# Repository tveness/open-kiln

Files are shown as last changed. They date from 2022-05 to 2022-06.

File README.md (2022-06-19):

# Open source kiln 

This project has grown out of the design (and hopefully construction in the near
future) of a kiln for heat-treating 80CrV2 steel.

The project is divided into two main parts: the driver circuit, and the kiln
itself. The driver circuit is assembled from readily-available modules arranged
on a custom PCB (we have a few spares and are happy to post you one of them),
whose design files and production-ready gerbers are in the repository.
The 

All designs are open: copying and improving is not only allowed, but encouraged.

## Driver circuit

### PCB

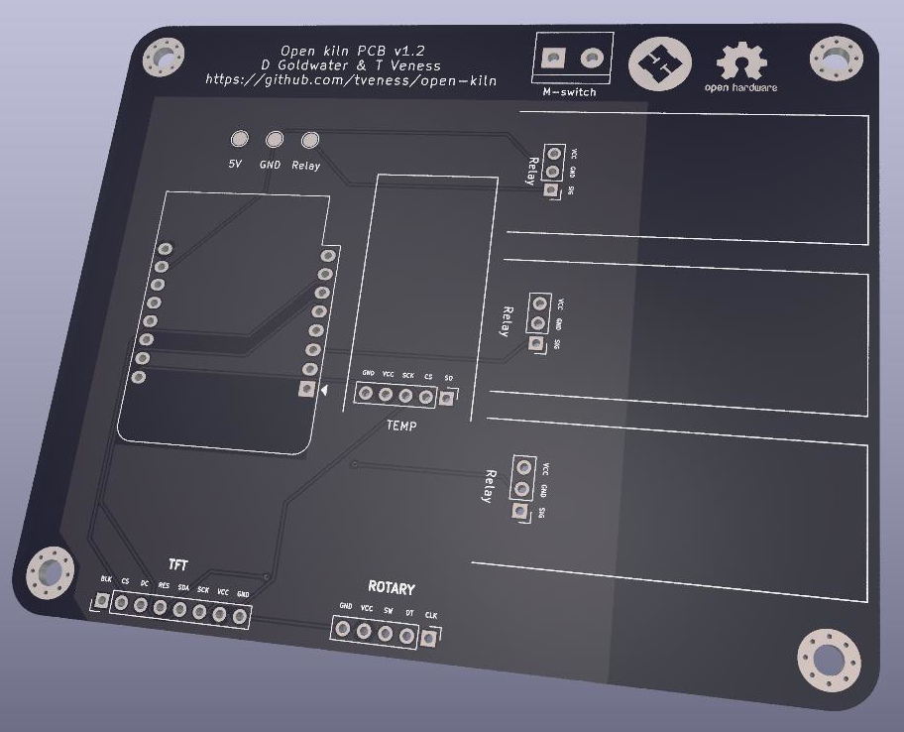
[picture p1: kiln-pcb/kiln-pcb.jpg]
Rendered PCB


We chose to use readily available modules both for protoyping purposes, and also
so reproduction is easy: the modules can all be purchased cheaply and the whole
assembly requires only through-hole soldering skills.

The components used are:

* Wemos D1 mini ESP8266 --- logic and power for board
* MAX6675 temperature module --- converts voltage from K-type thermocouple into signal which can be processed by ESP8266
* Rotary encoder --- input with rotating left and right, and depressing
* 0.96" TFT display
* 3x 5V relay modules

Some of these modules may come with headers already soldered, in which case you
may have to desolder and re-solder appropriate headers (all headers on PCB are
2.54mm/0.1" headers).

The PCB was designed with Kicad.

The logic of the design is that the temperature module measures the temperature
inside the kiln, and then according to the settings (TFT + rotary encoder
interface) the relays are activated to regulate the kiln temperature.

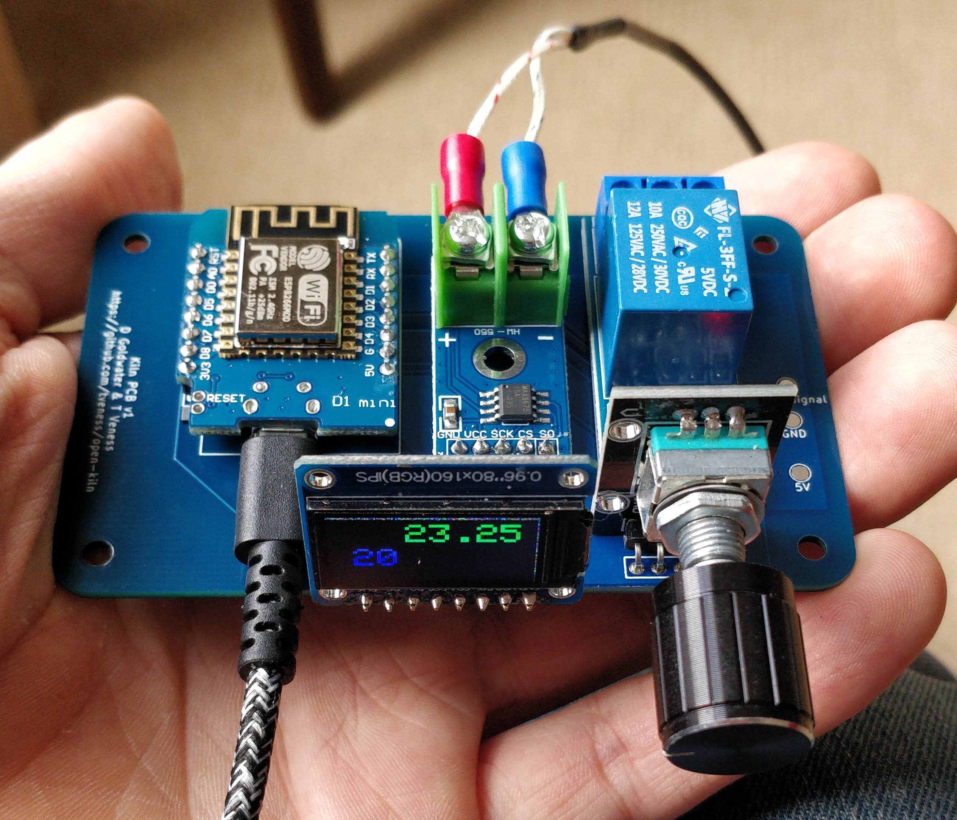
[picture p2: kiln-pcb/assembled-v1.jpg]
Assembled PCB (v1)


### Software

## Physical kiln

### Materials
We will need 27 vermiculite bricks for the main oven. 

### Firebrick enclosure
This is to be made from vermiculite firebricks. These are supplied in Imperial measurements; each brick has dimension:
$$ 8 \times 1 \times 4 ''.$$
The firebrick enclosure is to consist of two parts: the oven cavity, and a door. The measurements of these are as follows:

**Oven**:
Interior: $16 \times 8 \times 6''$

Exterior: $10 \times 17 \times 8$

**Door**:
The door is to be two bricks thick. The dimensions are:
$2 \times 10 \times 8$.

### Plaster casing
The plan is to cast a set of thick sheets with which to encase the oven. Since the door will be two bricks thick, there will be no outer casing for the door. The dimensions for these are to be:

Walls($\times 2$): $17 \times 10 \times d$

floor / ceiling ($\times 2$): $(17+d)\times(8+2d)\times d$

back ($\times 1$): $(8 + 2d)\times 10\times d$

where $d$ gives the thickness for the sheets. Provisionally, this is set at $1.5$''. 

### Approach 1:
Mix vermiculite to quick-set cement in a ratio $4:1$, add water until you can squeeze a fist and get a few drops out. 

### Metal case

### Resistive Elements
We use A1 kanthal wire, sourced from [here](https://www.ebay.co.uk/itm/322024532921). This has a resistivity of $1.8\Omega / m$. Aiming for $R = 13.2 \Omega$ per coil, we calculate:
$$d = 13.2 / 1.8 \\ = 7.3 $$
So that each element ought to be 7.3 $m$ long. 

### Wiring diagram
These images temporary, to be replaced
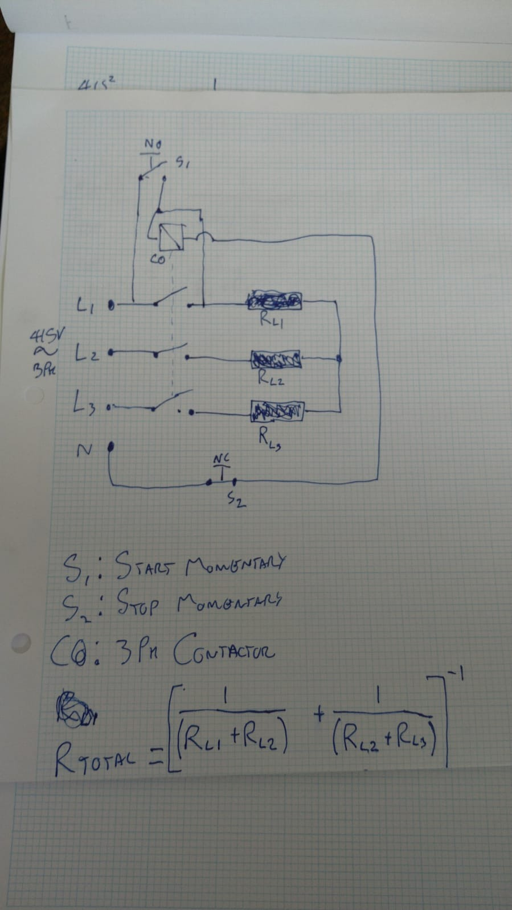
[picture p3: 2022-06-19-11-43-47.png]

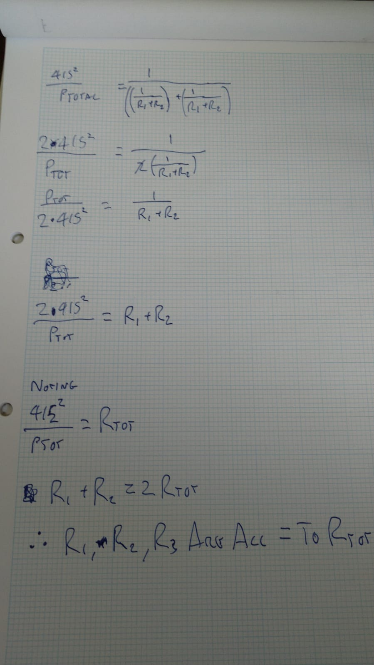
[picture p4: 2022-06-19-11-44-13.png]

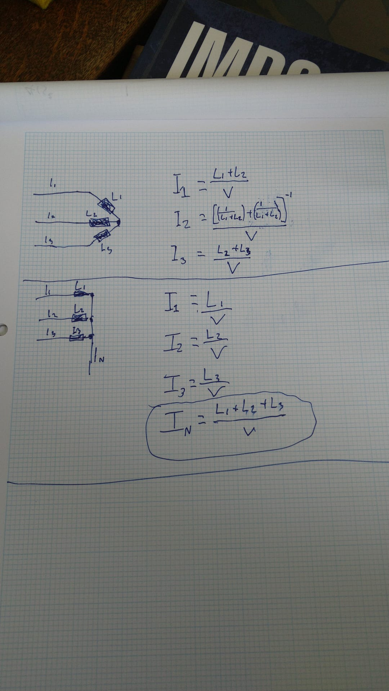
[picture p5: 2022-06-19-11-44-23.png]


### Safety considerations
We are to use:
- MCBs on each resistor element to isolate those in case of a short circuit. Also if one of the other coils fails, the power draw on the remaining coils would increase - the MCB here would save those coils before they burn out.
- Magnetic switch; this will leave a circuit *open* when the oven door is open, and *closed* when the oven door is closed. This means that there should be no power to the heating elements when the door is open. 
- Connector: This would function as a relay switch for the three phase power
- Relay: This would act as a pre-relay, and would be controlled directly by the PCB. (Expand this section)

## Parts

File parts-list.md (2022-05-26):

Electronics

* ESP8266 Wemos D1 mini
* MAX6675 temperature module
* Relay module
* TFT display 0.96"
* Rotary encoder

Kiln
* Kanthal wire
* Firebricks
* Metal enclosure

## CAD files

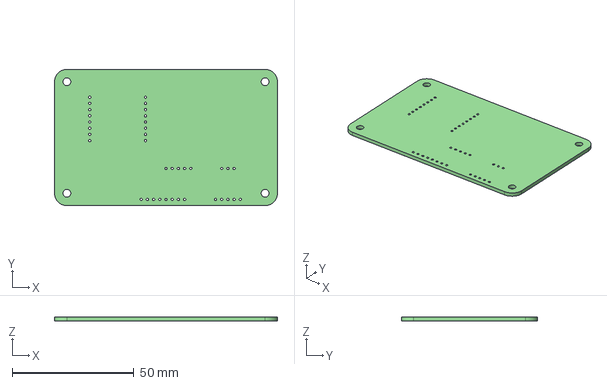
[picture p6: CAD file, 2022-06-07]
kiln-pcb/kiln-pcb.step
91.4 x 55.9 x 1.60 mm

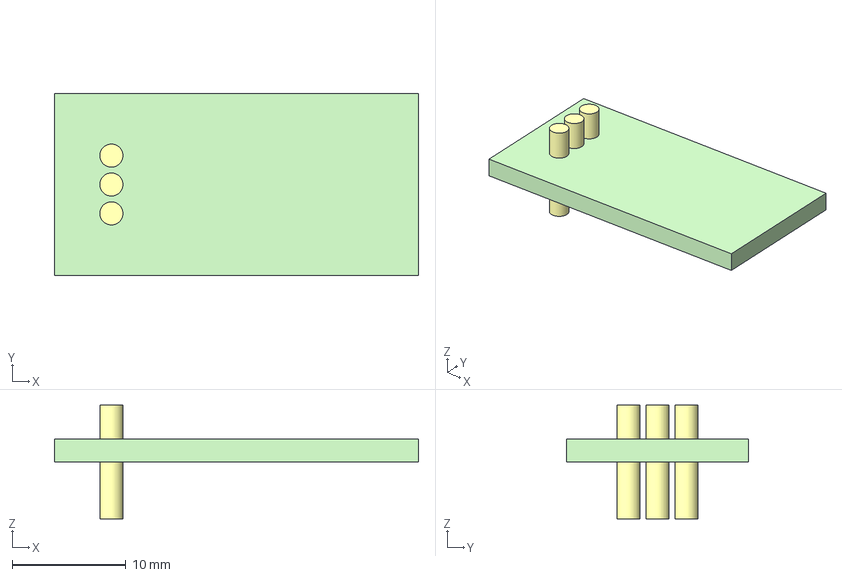
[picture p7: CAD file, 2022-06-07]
kiln-pcb/models/temp.FCStd
32.0 x 16.0 x 10.0 mm

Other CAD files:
kiln-pcb/models/temp-body.step

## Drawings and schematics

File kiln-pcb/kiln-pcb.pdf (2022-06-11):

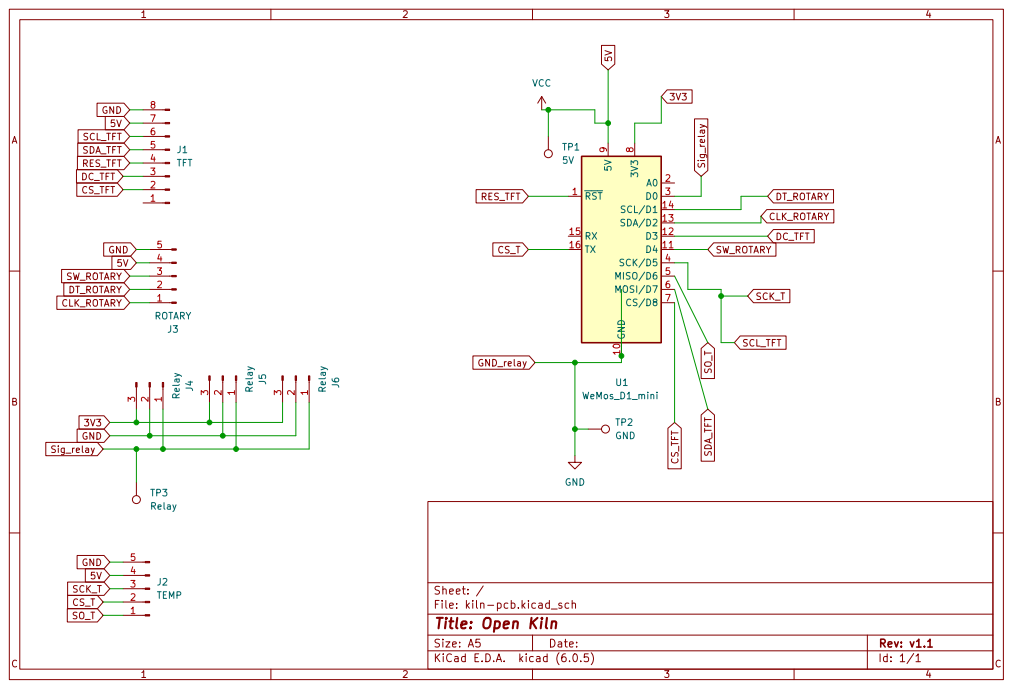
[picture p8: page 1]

File: kiln-pcb.kicad_sch Sheet: / 12345

Id: 1/1 Title: Open Kiln

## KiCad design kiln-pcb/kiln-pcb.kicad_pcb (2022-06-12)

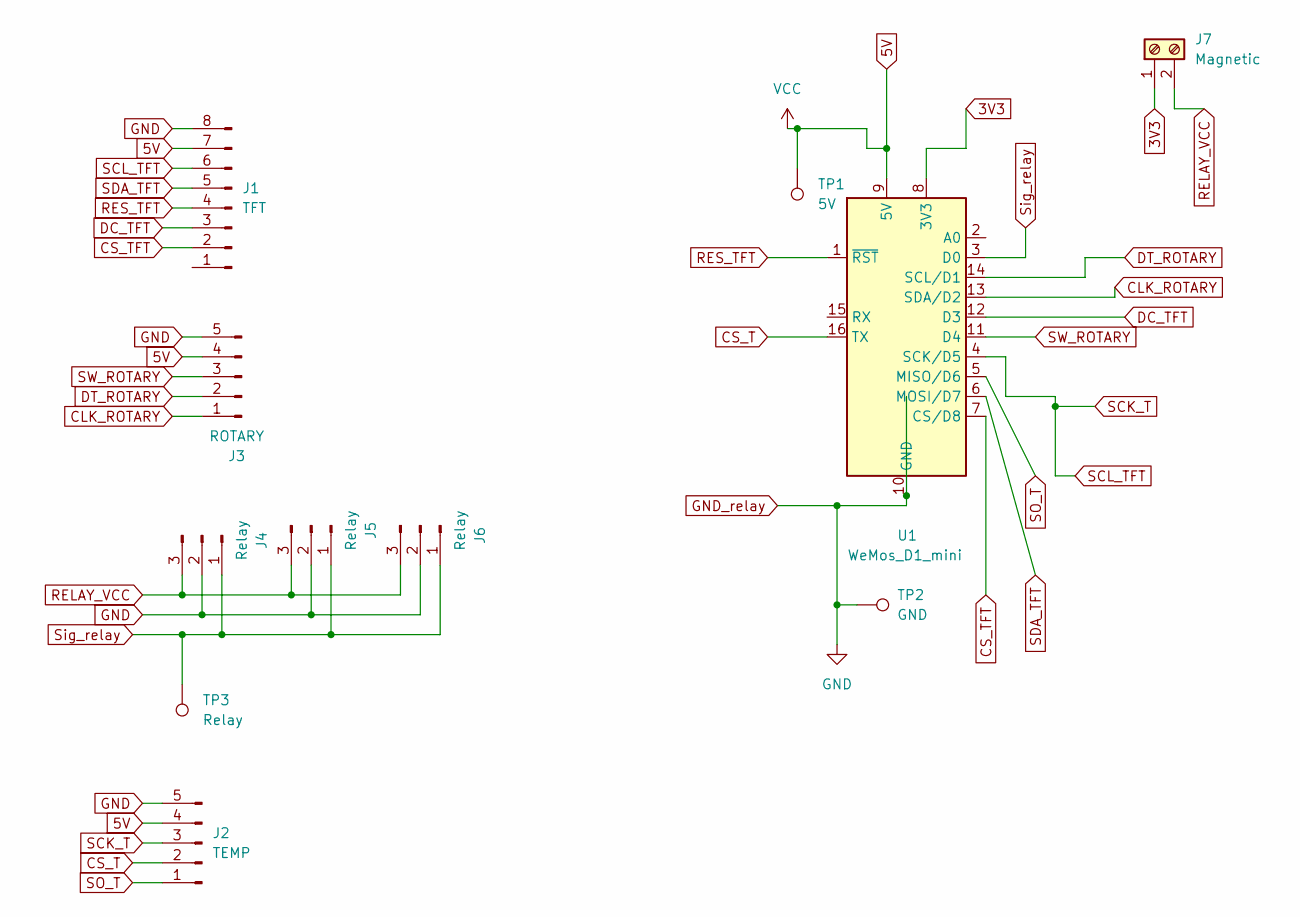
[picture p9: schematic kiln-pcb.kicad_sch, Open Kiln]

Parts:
J1: TFT; PinHeader_1x08_P2.54mm_Vertical
J2: TEMP; PinHeader_1x05_P2.54mm_Vertical
J3: ROTARY; PinHeader_1x05_P2.54mm_Vertical
J4, J5, J6: Relay; PinHeader_1x03_P2.54mm_Vertical
J7: Magnetic; TerminalBlock_bornier-2_P5.08mm
TP1: 5V; TestPoint_Pad_D2.0mm
TP2: GND; TestPoint_Pad_D2.0mm
TP3: Relay; TestPoint_Pad_D2.0mm
U1: WeMos_D1_mini; WEMOS_D1_mini_light

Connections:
3V3: J7.1, U1.8 (3V3); also elsewhere on the board
5V: J1.7, J2.4, J3.4, TP1.1, U1.9 (5V)
CLK_ROTARY: J3.1, U1.13 (SDA/D2)
CS_T: J2.2, U1.16 (TX)
CS_TFT: J1.2, U1.7 (CS/D8)
DC_TFT: J1.3, U1.12 (D3)
DT_ROTARY: J3.2, U1.14 (SCL/D1)
GND: J1.8, J2.5, J3.5, J4.2, J5.2, J6.2, TP2.1, U1.10 (GND)
RELAY_VCC: J4.3, J5.3, J6.3, J7.2; also elsewhere on the board
RES_TFT: J1.4, U1.1 (~RST)
SCK_T: J1.6, J2.3, U1.4 (SCK/D5)
SDA_TFT: J1.5, U1.6 (MOSI/D7)
SO_T: J2.1, U1.5 (MISO/D6)
SW_ROTARY: J3.3, U1.11 (D4)
Sig_relay: J4.1, J5.1, J6.1, TP3.1, U1.3 (D0)

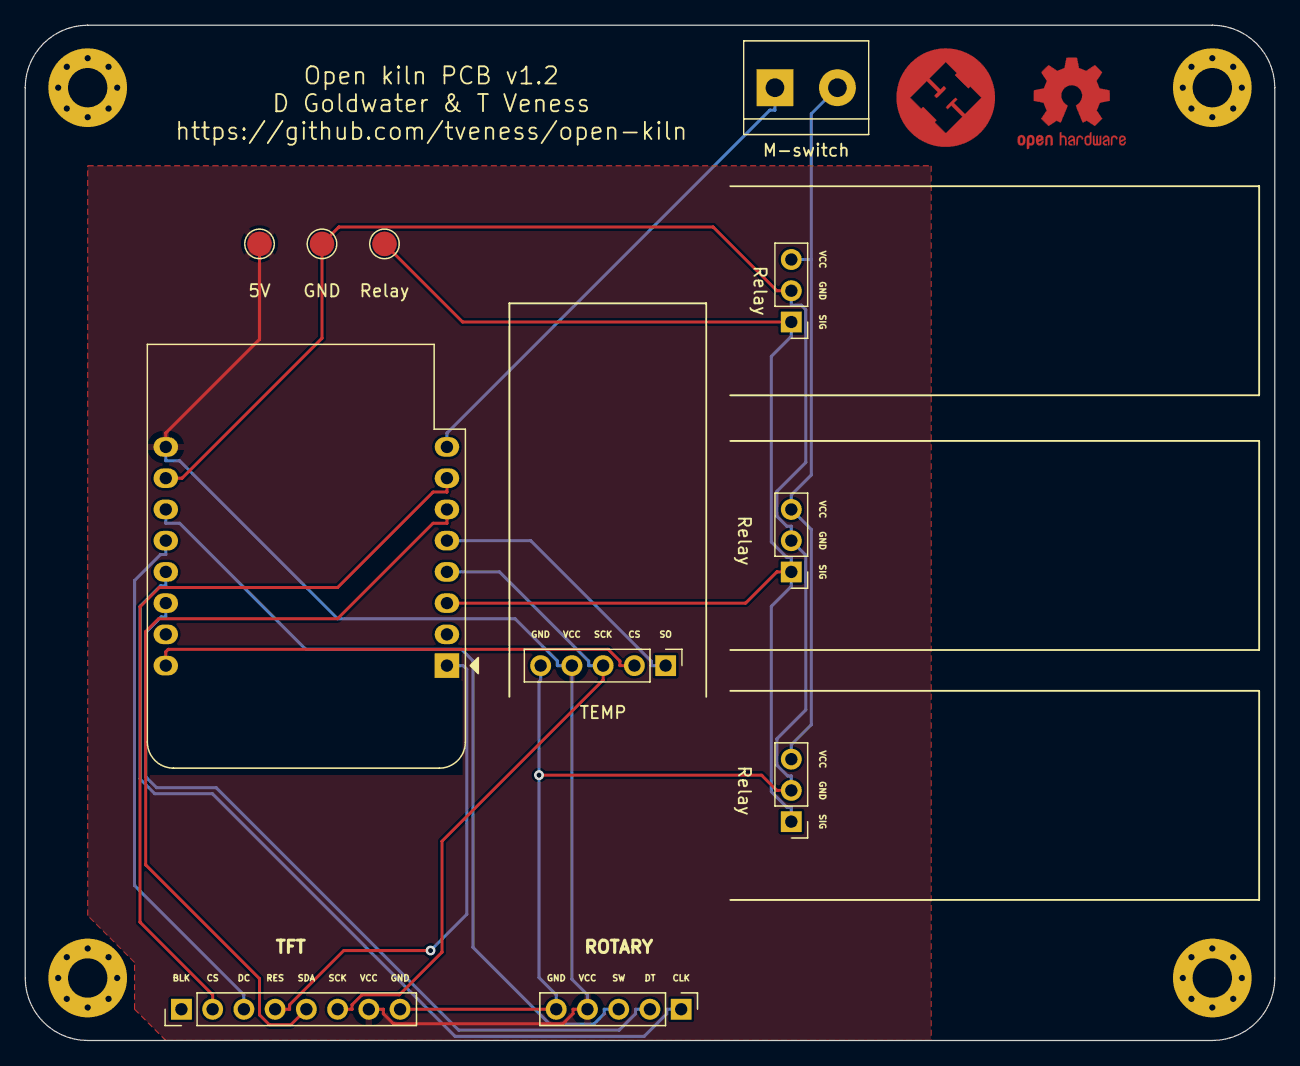
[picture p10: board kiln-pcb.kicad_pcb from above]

Board: 2 copper layers, 101.6 x 82.6 mm, 17 parts (0 on the bottom side), 15 nets.

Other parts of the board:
H1, H2, H3, H4: MountingHole_3.2mm_M3_Pad_Via
HS_LOGO: Val**; hackspace_small
M-switch: Magnetic; TerminalBlock_bornier-2_P5.08mm
OSHW_LOGO: OSHW-Logo2_9.8x8mm_Copper

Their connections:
3V3: M-switch.1; also elsewhere on the board
RELAY_VCC: M-switch.2; also elsewhere on the board

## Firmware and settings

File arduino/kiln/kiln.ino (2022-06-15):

#include <Arduino.h>
#include <RotaryEncoder.h>
#include "max6675.h"
#include <Adafruit_GFX.h>    // Core graphics library
#include <Adafruit_ST7735.h> // Hardware-specific library for ST7735
//#include <Adafruit_ST7789.h> // Hardware-specific library for ST7789
#include <SPI.h>
#include <Bounce2.h>

int thermoDO = D6;
int thermoCS = D8;
int thermoCLK = D5;
char Tbuffer[50];
char set_buffer[50];
bool short_press=false;
bool long_press=false;
bool long_press_action=false;


class pid {
  float duty;
  float kp;
  float ki;
  float kd;
  float e_p;
  float last_time;

  float i_output;
  float i_max;
  float i_offset;
  float last_actual;
  
  
  public:
    float get_duty(void);
    pid (float, float, float, float);
    float update_duty(float, float);
};

pid::pid(float kp_init,float ki_init,float kd_init, float i_offset_init){
  kp=kp_init;
  ki=ki_init;
  kd=kd_init;
  i_output=0;
  i_offset=i_offset_init;
  i_max = 0.1;
  last_actual=0;
  last_time=millis();
  duty=0.0;
  e_p=0.0;
}

float pid::get_duty() {
  return duty;
}

float pid::update_duty(float target, float actual){
  float now=millis();
  float dt = (now - last_time)/1000.0;
  
  float error=target - actual;
  

 
  i_output += error * ki*dt;
  if (i_output > i_max) {
    i_output = i_max;
  }
  if (i_output < -i_max) {
    i_output = -i_max;
  }
  float d_out = kd*(actual-last_actual)/dt;
  Serial.print("p:");
  Serial.print(kp*error);
  Serial.print(",i:");
  Serial.print(i_output);
  Serial.print(",d:");
  Serial.print(d_out);
  float output = kp*error + i_output + d_out;
  

  last_actual = actual;
  last_time=now;

  if (output < 0) {
    output= 0.0;
  }
  else if (output > 1) {
    output= 1.0;
  }
  duty = output;
  return output;
 
  
}



MAX6675 thermocouple(thermoCLK, thermoCS, thermoDO);

/*************************************/


#define TFT_CS         D8
//#define TFT_RST        RST
#define TFT_RST         -1                                          //And connect to arduino reset
#define TFT_DC         D3
#define TFT_MOSI D7  // Data out
#define TFT_SCLK D5  // Clock out

// For ST7735-based displays, we will use this call
//Adafruit_ST7735 tft = Adafruit_ST7735(TFT_CS, TFT_DC, TFT_RST);
  Adafruit_ST7735 tft = Adafruit_ST7735(TFT_CS, TFT_DC, TFT_MOSI, TFT_SCLK, TFT_RST);

/***************************/

/////////////////////////////////////////////////////////////////


#define PIN_IN1 D1
#define PIN_IN2 D2
#define BOUNCE_PIN D4

#define LED_PIN D0

#define T_OFFSET 20
#define T_STEP 5
#define T_MIN 5
#define T_MAX 1200

#define ROTARY_MIN ( (T_MIN-T_OFFSET)/T_STEP )
#define ROTARY_MAX ( (T_MAX-T_OFFSET)/T_STEP )

RotaryEncoder *encoder = nullptr;
Bounce bounce = Bounce();


IRAM_ATTR void checkPosition()
{
  encoder->tick(); // just call tick() to check the state.

  if ( encoder->getPosition() < ROTARY_MIN){
    encoder->setPosition(ROTARY_MIN);
  }
  if ( encoder->getPosition() > ROTARY_MAX){
    encoder->setPosition(ROTARY_MAX);
  }
}



/////////////////////////////////////////////////////////////////
pid pidc(0.01,1e-5,-0.01,0.0);
unsigned long tt;
int pos = -1;
float T = T_OFFSET+10;
unsigned long duty_period = 10;//duty period in seconds
unsigned long duty_cutoff_lower=1.0;
unsigned long duty_cutoff_higher = 59.0;
unsigned long duty_counter = 0.0;
float duty_cycle = 0.0;
void setup() {
  bounce.attach( BOUNCE_PIN, INPUT );
  bounce.interval(5); // interval in ms
  
  
  Serial.begin(9600);

  
  pinMode(LED_PIN, OUTPUT);
  //analogWrite(LED_PIN,0 );
  digitalWrite(LED_PIN,HIGH);
  Serial.println("MAX6675 test");
  //SPI.begin();
  
  tft.initR(INITR_MINI160x80);  // Init ST7735S mini display
  
  Serial.println(F("Initialized"));

  tt = millis();
  tft.invertDisplay(true);
  tft.fillScreen(ST77XX_BLACK);
  tft.setRotation(1);

// wait for MAX chip to stabilize
  delay(500);
   // use TWO03 mode when PIN_IN1, PIN_IN2 signals are both LOW or HIGH in latch position.
  encoder = new RotaryEncoder(PIN_IN1, PIN_IN2, RotaryEncoder::LatchMode::TWO03);

  // register interrupt routine
  attachInterrupt(digitalPinToInterrupt(PIN_IN1), checkPosition, CHANGE);
  attachInterrupt(digitalPinToInterrupt(PIN_IN2), checkPosition, CHANGE);


  // LED
  duty_counter = millis();

  pinMode(LED_PIN, OUTPUT);
  digitalWrite(LED_PIN,HIGH);
  write_set(0,&pos);
  
}




void loop() {
  // basic readout test, just print the current temp
   //tft.fillScreen(ST77XX_BLACK);


  bounce.update();
  int debouncedState = bounce.read();
  
   if ( debouncedState == LOW && bounce.currentDuration() > 3 ) {
   short_press = true;
   
  } 
  if (debouncedState == LOW && bounce.currentDuration() > 1000 && !long_press){

    long_press = true;
    long_press_action = true;
    short_press = false;
  }

  if (debouncedState == HIGH && long_press){
    long_press=false;
    short_press=false;
  }

  if (long_press_action) {
    Serial.println("LONG PRESS");
    long_press_action=false;
  }
  
 
  if (debouncedState == HIGH && short_press ){
    short_press = false;
    Serial.println("CLICK!");
  }


  encoder->tick(); // just call tick() to check the state.

  unsigned long now = millis();
  unsigned long elapsed = now - tt;

  
  // Reset counter every period
  if ( (now-duty_counter) > duty_period*1000) {
    duty_counter =now;
    digitalWrite(LED_PIN,LOW);
  }
  
  if ( (now - duty_counter) > duty_cycle * duty_period*1000 ){
   digitalWrite(LED_PIN,HIGH); 
  }

  float target=pos*T_STEP+T_OFFSET;
   
   if (elapsed > 500 ){
    //delay(1000);
    T = thermocouple.readCelsius();
    write_T(&tt);
    duty_cycle = pidc.update_duty(target, T);
    Serial.print(",C:");
    Serial.print(T);
    Serial.print(",target:"); 
    Serial.print(target);
   //Serial.println(thermocouple.readCelsius());
   //Serial.print(", F:");
   //Serial.print(thermocouple.readFahrenheit());
   Serial.print(",duty:");
    Serial.println(duty_cycle);

    
    
    }
  

  
  /*
  if (target > T) {
    //int mag = 255*(target-T)*(target-T)/T /T;
    //mag = mag>0?mag:0;
    //analogWrite(LED_PIN,(mag>255)?255:mag );
    digitalWrite(LED_PIN,LOW);
    
  }
  else {
    //analogWrite(LED_PIN,0)
    digitalWrite(LED_PIN,HIGH);
  }
  */
 
 encoder->tick(); // just call tick() to check the state.

 int newPos = encoder->getPosition();
 write_set(newPos,&pos);
  
  

   // For the MAX6675 to update, you must delay AT LEAST 250ms between reads!
   //delay(1000);
}

void write_T(unsigned long *tt){
   
   tft.setTextColor(ST77XX_GREEN,ST77XX_BLACK);
   tft.setTextSize(3);  
   tft.setCursor(60, 10);
   tft.print(" ");
   //tft.print(T,2);
   tft.setCursor(60,10);
   char t_buf[10];
   sprintf(t_buf,"%.2f",T);
   tft.print(t_buf);
   //tft.print(T,2);
   *tt=millis();
   

}

void write_set(int newPos, int *pos){
if (*pos != newPos) {
/*    Serial.print("pos:");
    Serial.print(newPos);
    Serial.print(" dir:");
    Serial.println((int)(encoder->getDirection()));
   
     */
  *pos = newPos;
   
   
  tft.setTextColor(ST77XX_RED,ST77XX_BLACK);
   tft.setTextSize(3);  
   tft.setCursor(20,40);
   tft.print(" ");
   tft.setCursor(20,40);
   int p=*pos*5+20;
   //tft.print((p>0)?p:0,DEC);
  sprintf(set_buffer,"%d ",p);
   tft.print((char *) set_buffer);
    } // if
}

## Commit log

2022-06-07 Added simple PID for relay
    [kiln-pcb.kicad_pcb, kiln-pcb.kicad_sch, kiln-pcb.step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]
2022-06-11 PCB v1.1
    [kiln-pcb-B_Cu.gbr, kiln-pcb-B_Mask.gbr, kiln-pcb-B_Paste.gbr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]
2022-06-11 Fixed "kerning"
    [kiln-pcb-B_Cu.gbr, kiln-pcb-B_Mask.gbr, kiln-pcb-B_Paste.gbr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]
2022-06-11 Basic README update
    [kiln-pcb-B_Cu.gbr, kiln-pcb-B_Mask.gbr, kiln-pcb-B_Paste.gbr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]
2022-06-11 Assembled pic
2022-06-12 Added magnetic switch interrupt
    [kiln-pcb-B_Cu.gbr, kiln-pcb-B_Mask.gbr, kiln-pcb-B_Paste.gbr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]
2022-06-15 New PCB image
2022-06-19 Added basic dimensions and resistor specs
